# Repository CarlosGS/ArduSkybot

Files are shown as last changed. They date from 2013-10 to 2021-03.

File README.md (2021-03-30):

ArduSkybot  
=====  

**Low cost educational printbot based on Arduino.**  

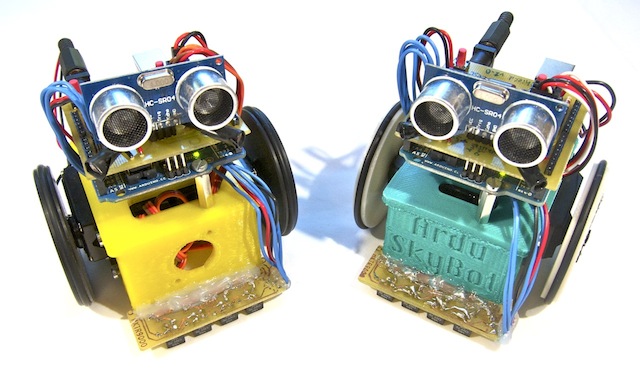
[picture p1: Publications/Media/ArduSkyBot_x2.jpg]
  

Here you will find:  
 * All files and information necessary to build an ArduSkybot.  
 * Arduino code examples for the robot.  
 * Documentation and workshop slides.  
 * Research work about the ArduSkybot (in spanish).  
 * Source files for everything :)  

Video  
--  
You can see the robot being used in the 2012 Summer Workshop:  
**<http://www.youtube.com/watch?v=2o3PmDZZxAQ>**  

License  
--
License (_unless other specified_): **Attribution - Share Alike - Creative Commons (<http://creativecommons.org/licenses/by-sa/3.0/>)**  

Author  
--
Carlos García Saura

Acknowledgement  
--
Based on the MiniSkybot by:  
 * **Juan González Gómez "Obijuan"** (<http://www.iearobotics.com/wiki/index.php?title=Juan_Gonzalez:Main>)  
 * **Alberto Valero Gómez** (<http://iearobotics.com/alberto/doku.php>)  

ArduSkybot  
--
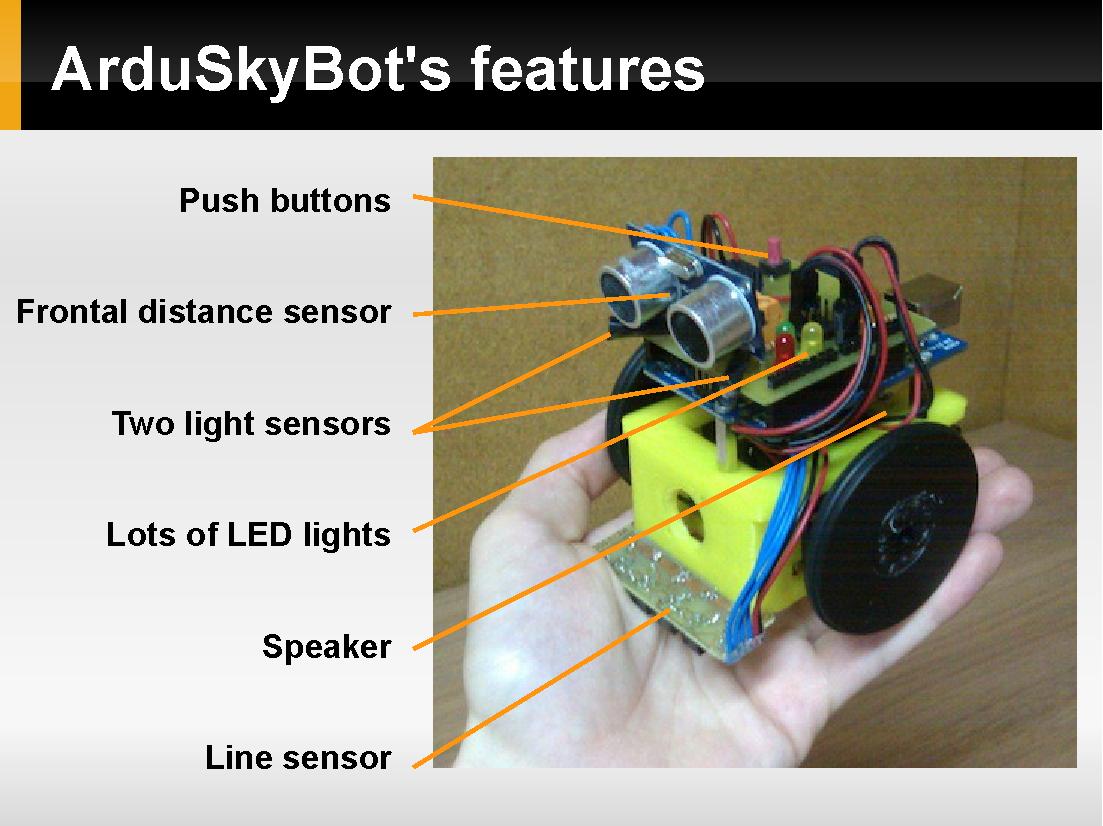
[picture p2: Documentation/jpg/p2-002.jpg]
  
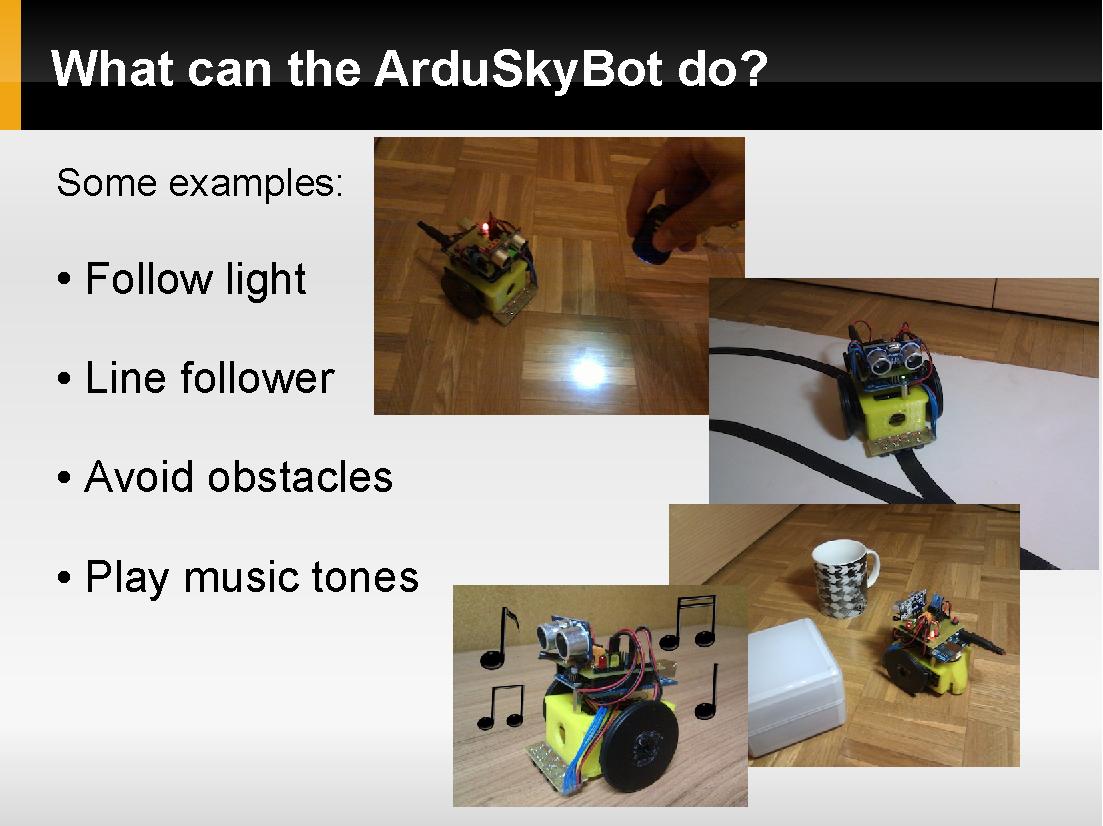
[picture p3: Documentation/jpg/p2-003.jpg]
  
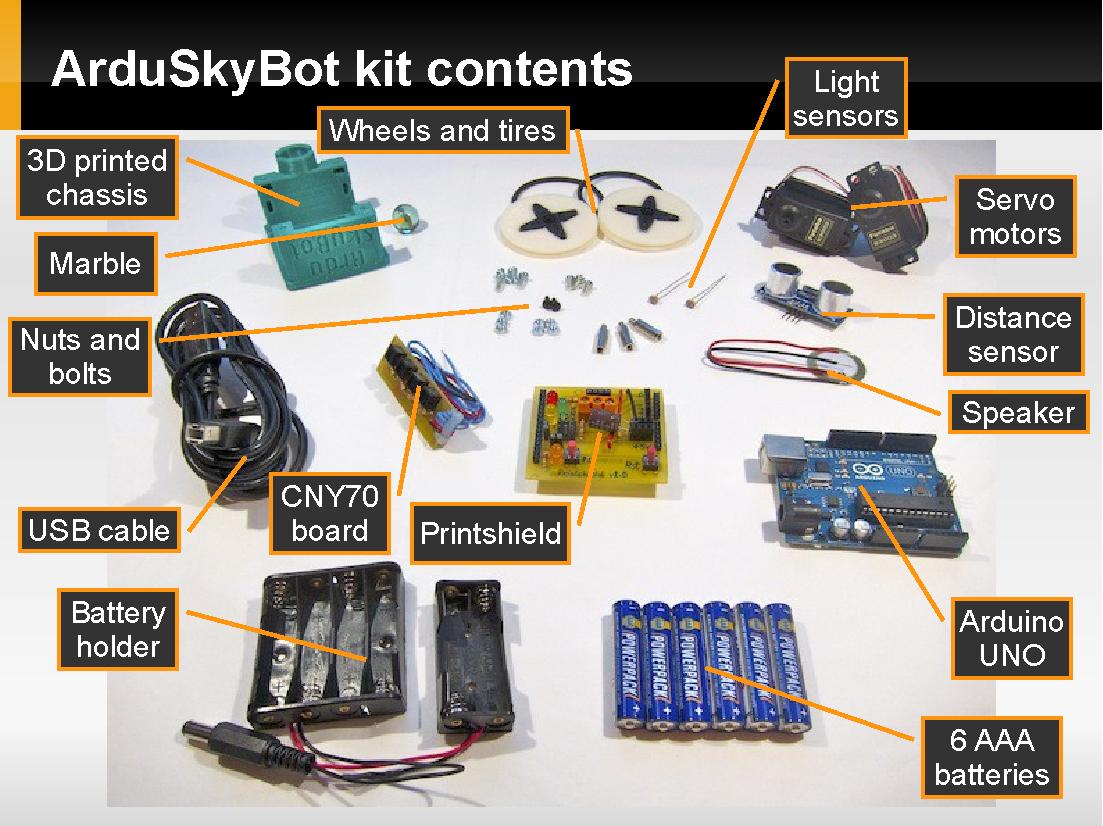
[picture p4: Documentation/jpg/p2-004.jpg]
  
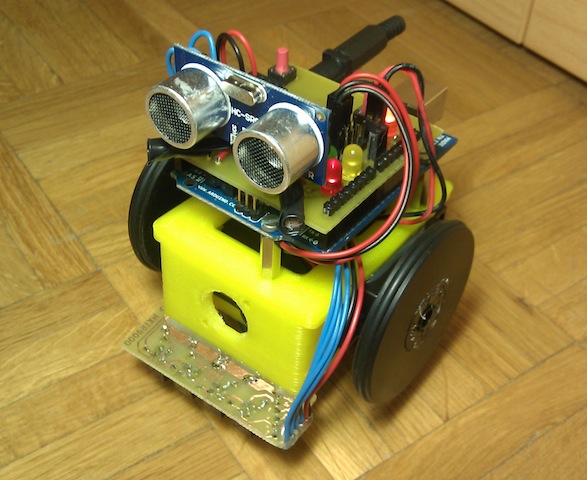
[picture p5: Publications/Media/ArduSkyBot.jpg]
  

Disclaimer  
--
This hardware/software is provided "as is", and you use the hardware/software at your own risk. Under nocircumstances shall any author be liable for direct, indirect, special, incidental, or consequential damages resulting from the use, misuse, or inability to use this hardware/software, even if the authors have been advised of the possibility of such damages.

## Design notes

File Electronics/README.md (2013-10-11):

Electronics for the ArduSkybot  
=====  

_Full instructions (summary below these lines):_
* _Printshield: <https://github.com/carlosgs/ArduSkybot/tree/master/Documentation/1%20-%20Introduction> and <https://github.com/carlosgs/ArduSkybot/tree/master/Documentation/2%20-%20Robot%20assembly>_
* _Line sensor: <https://github.com/carlosgs/ArduSkybot/tree/master/Documentation/4%20-%20Line%20sensor>_

The Printshield for Arduino  
=====  
  
  
  
  

The line sensor board  
=====  
  
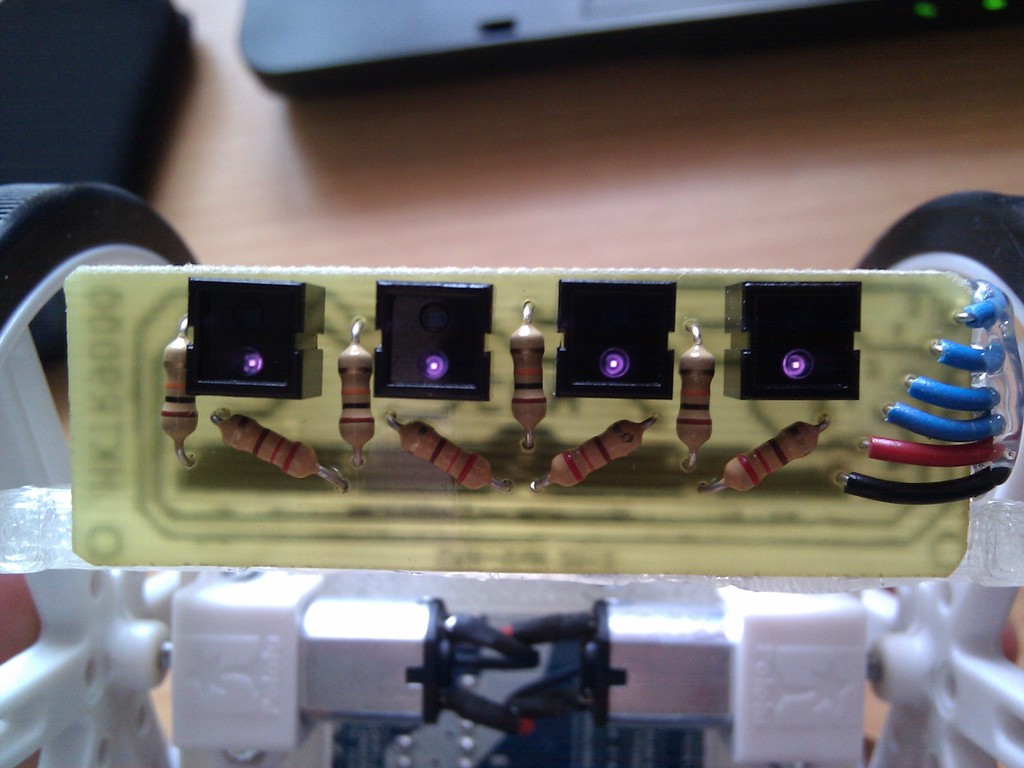
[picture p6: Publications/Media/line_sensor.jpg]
  
  
  


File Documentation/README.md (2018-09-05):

Documentation for the ArduSkybot  
=====  

**In the different folders you will find the instructions for each part of the assembly**  

  

These slides were used in a workshop in Summer 2012, the full description of the workshop is hosted here:  
<https://web.archive.org/web/20150204114811/http://carlosgs.es/2012-summer-workshop>  

Workshop contents  
--  
These slides were used in a workshop in Summer 2012, the full description of the workshop is hosted here: <https://web.archive.org/web/20150204114811/http://carlosgs.es/2012-summer-workshop>  

1. Introduction to robotics with Arduino  
    * Lesson contents:  
        * Basic components of a robot.  
        * What is Arduino and how to program it.  
        * Meet the ArduSkyBot!  
        * You will play music and make LED's blink!  
    * Code (LED blink, tone melody, light harp, servo motor turn and bonus)  
2. Assembling the ArduSkyBot  
    * Lesson contents:  
        * Components of our robot  
        * How to build the ArduSkyBot!  
        * Simple programming examples  
        * You will program your own sequences!  
    * Code (simple ArduSkyBot demo)  
3. Programming the ArduSkyBot  
    * Lesson contents:  
        * Better understanding on how to program for Arduino.  
        * How to use the distance sensor to avoid objects.  
        * Usage of the light sensors to make the ArduSkyBot follow light!  
        * Advanced: while following light, avoid obstacles!  
    * Code  
4. Using the line sensor  
    * Lesson contents:  
        * What is the line sensor and how it works.  
        * How to assemble and test the line sensor.  
        * You will make the ArduSkyBot follow a line!  
        * Advanced: while following a line, avoid obstacles!  
    * Code  

**Jpg images were generated using the following commands:**  
 * gs -sOutputFile=p1-%03d.jpg -dNOPAUSE -dSAFER -sDEVICE=jpeg -dBATCH -r100 2012\ Lesson\ 1\ -\ Introduction\ to\ robotics\ with\ Arduino.pdf
 * gs -sOutputFile=p2-%03d.jpg -dNOPAUSE -dSAFER -sDEVICE=jpeg -dBATCH -r100 2012\ Lesson\ 2\ -\ Assembling\ the\ ArduSkyBot.pdf
 * gs -sOutputFile=p3-%03d.jpg -dNOPAUSE -dSAFER -sDEVICE=jpeg -dBATCH -r100 2012\ Lesson\ 4\ -\ Using\ the\ line\ sensor.pdf

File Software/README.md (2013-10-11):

Software examples for the ArduSkybot  
=====  

These are the examples used for the 2012 Summer Workshop.  

Workshop contents  
--  
1. Introduction to robotics with Arduino  
    * Lesson contents:  
        * Basic components of a robot.  
        * What is Arduino and how to program it.  
        * Meet the ArduSkyBot!  
        * You will play music and make LED's blink!  
    * Code (LED blink, tone melody, light harp, servo motor turn and bonus)  
2. Assembling the ArduSkyBot  
    * Lesson contents:  
        * Components of our robot  
        * How to build the ArduSkyBot!  
        * Simple programming examples  
        * You will program your own sequences!  
    * Code (simple ArduSkyBot demo)  
3. Programming the ArduSkyBot  
    * Lesson contents:  
        * Better understanding on how to program for Arduino.  
        * How to use the distance sensor to avoid objects.  
        * Usage of the light sensors to make the ArduSkyBot follow light!  
        * Advanced: while following light, avoid obstacles!  
    * Code  
4. Using the line sensor  
    * Lesson contents:  
        * What is the line sensor and how it works.  
        * How to assemble and test the line sensor.  
        * You will make the ArduSkyBot follow a line!  
        * Advanced: while following a line, avoid obstacles!  
    * Code  

ArduSkyBot demo code  
--  
Code for demonstrating the basic functionality of the ArduSkyBot.

1. At the beginning the robot will make a sound and the orange LED will light up.
2. Then you can select an option (with the push button):
    * Orange LED: Distance harp
    * Red LED: Line follower
    * Green LED: Light follower (with obstacle avoidance)
    * Yellow LED: Obstacle avoidance
3. Wait for 5 seconds, the robot will make a sound and the selected LED will blink.
4. Press the button to launch the program.

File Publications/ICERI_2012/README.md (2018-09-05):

Publication for ICERI 2012  
=====  

_Carlos García-Saura, Juan González-Gómez (2012) **"Low cost educational platform for robotics, using open-source 3D printers and open-source hardware"**, ICERI2012 Proceedings, pp. 2699-2706. ISBN: 978-84-616-0763-1_  

<https://web.archive.org/web/20150204114839/http://carlosgs.es/Printbots-for-education-at-ICERI-2012>  

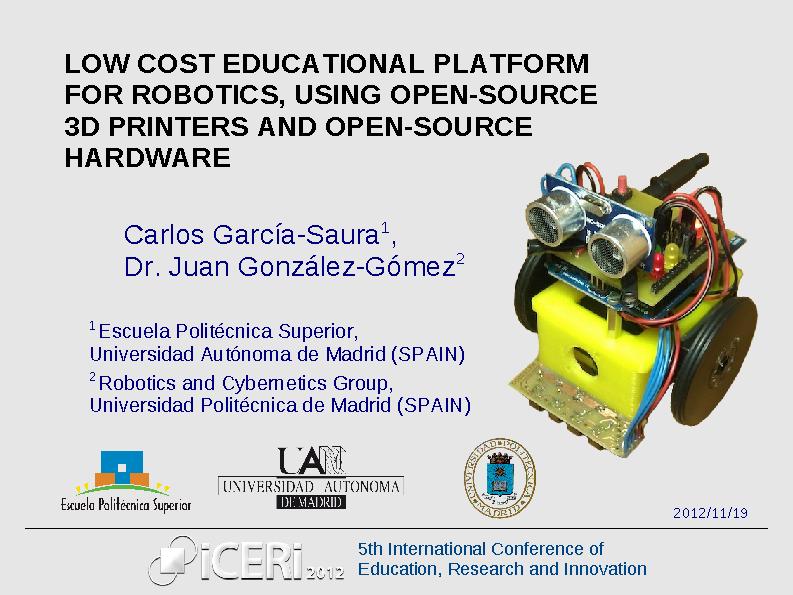
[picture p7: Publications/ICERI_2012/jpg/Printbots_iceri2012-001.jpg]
  
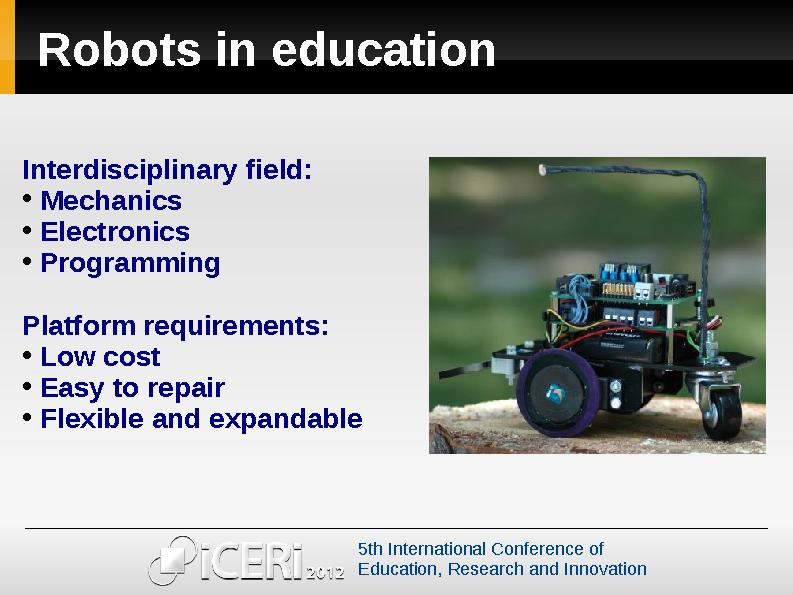
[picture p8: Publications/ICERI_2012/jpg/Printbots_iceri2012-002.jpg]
  
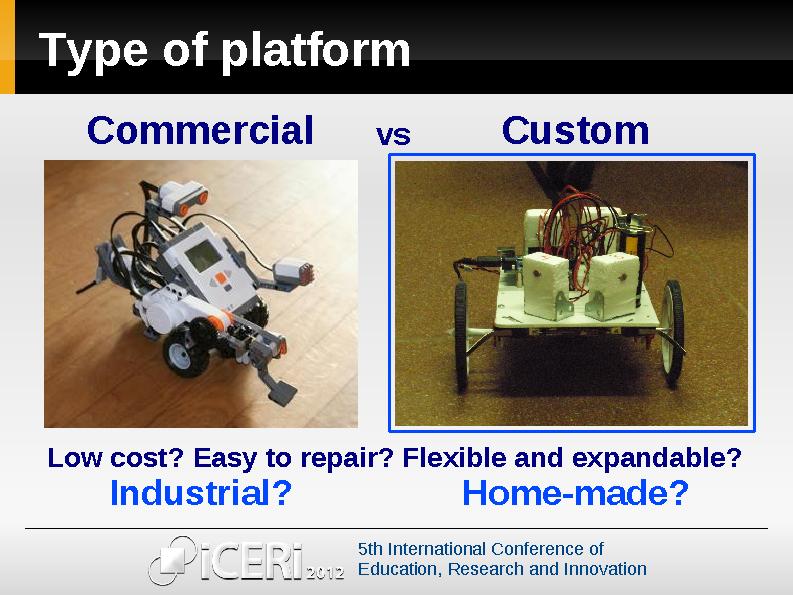
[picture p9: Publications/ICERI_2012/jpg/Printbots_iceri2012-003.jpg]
  
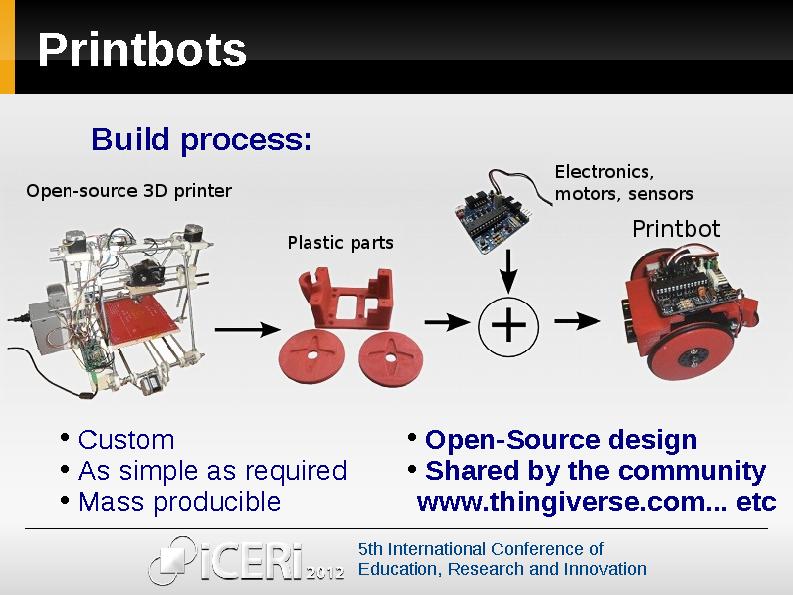
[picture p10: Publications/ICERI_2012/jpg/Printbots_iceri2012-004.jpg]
  
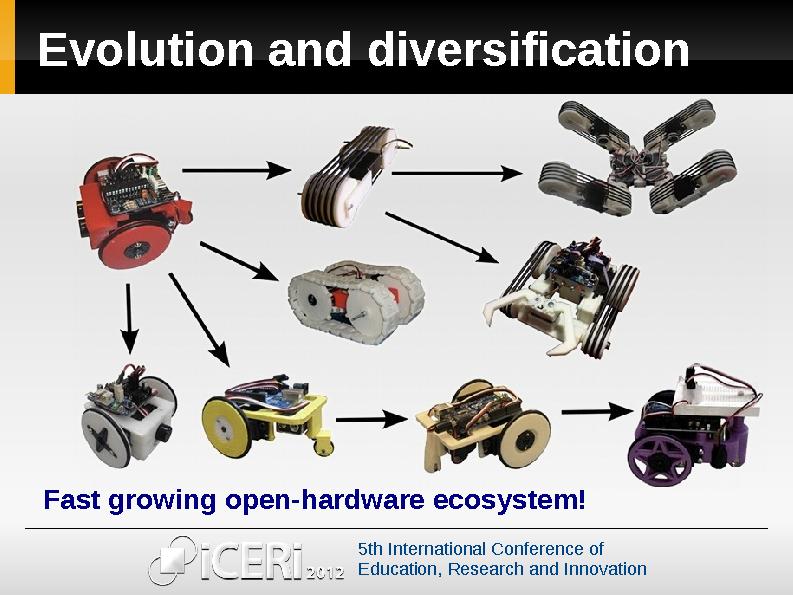
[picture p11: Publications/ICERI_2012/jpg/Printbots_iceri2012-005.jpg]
  
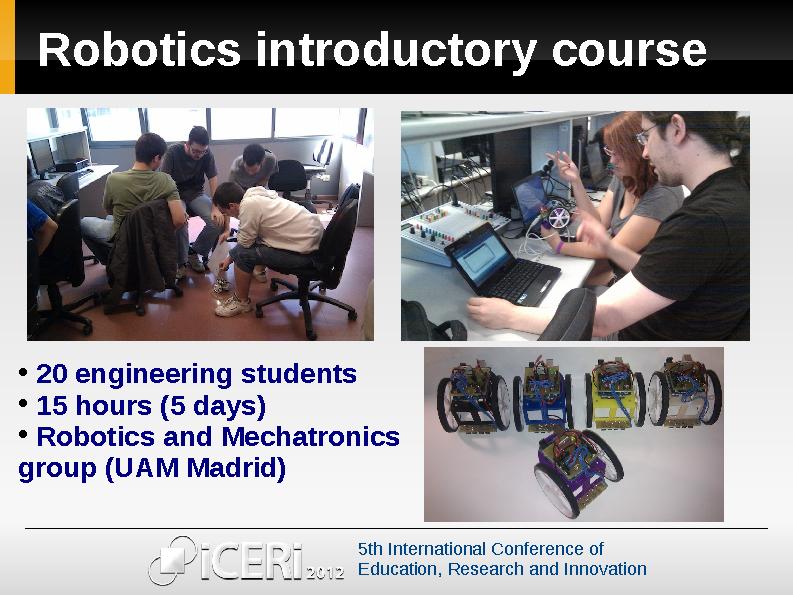
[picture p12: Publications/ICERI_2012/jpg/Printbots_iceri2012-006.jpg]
  
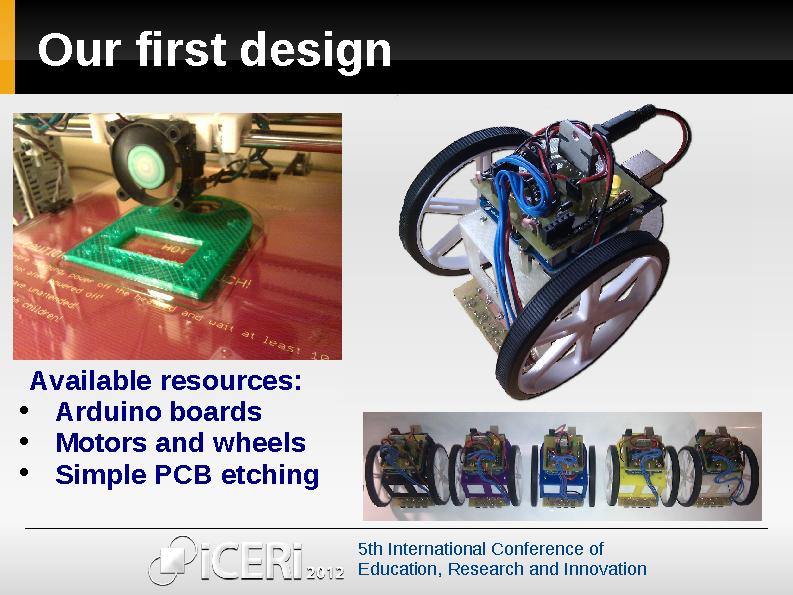
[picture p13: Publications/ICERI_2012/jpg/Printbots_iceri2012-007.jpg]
  
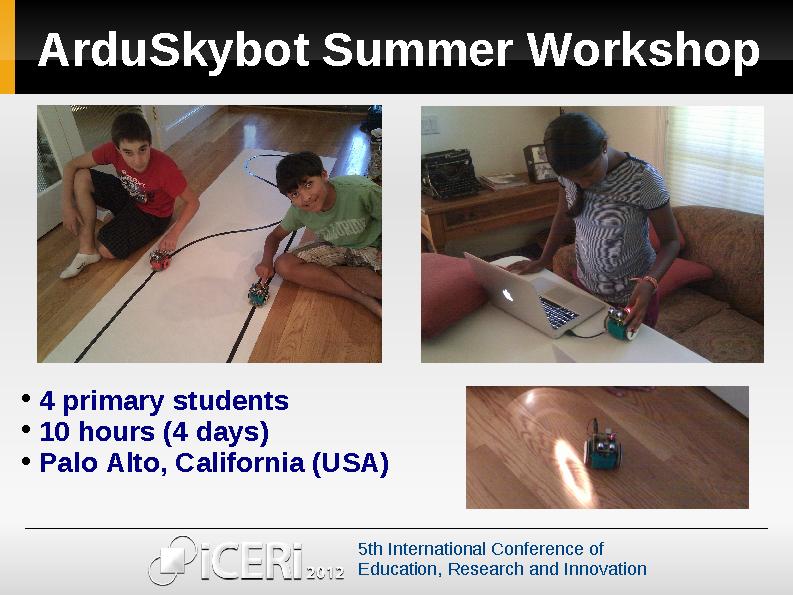
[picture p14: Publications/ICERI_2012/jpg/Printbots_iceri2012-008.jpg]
  
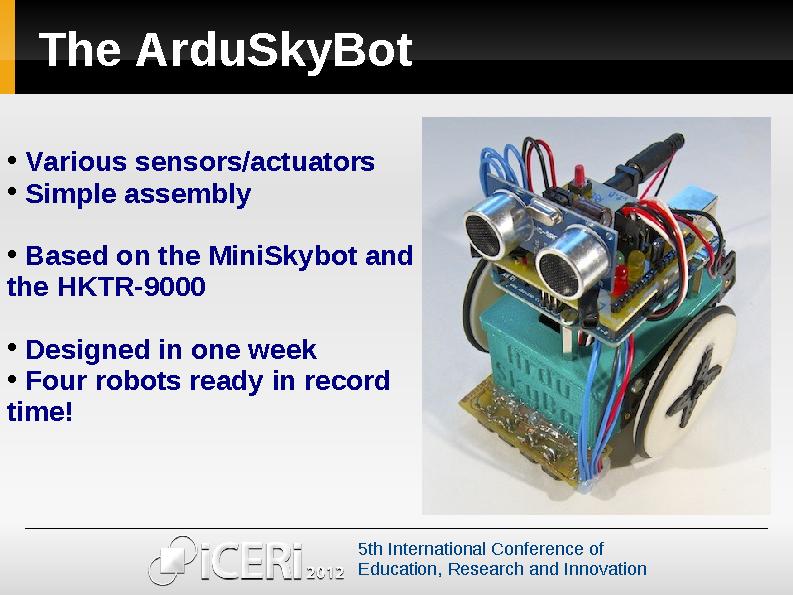
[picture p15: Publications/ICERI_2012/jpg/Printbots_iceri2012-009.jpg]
  
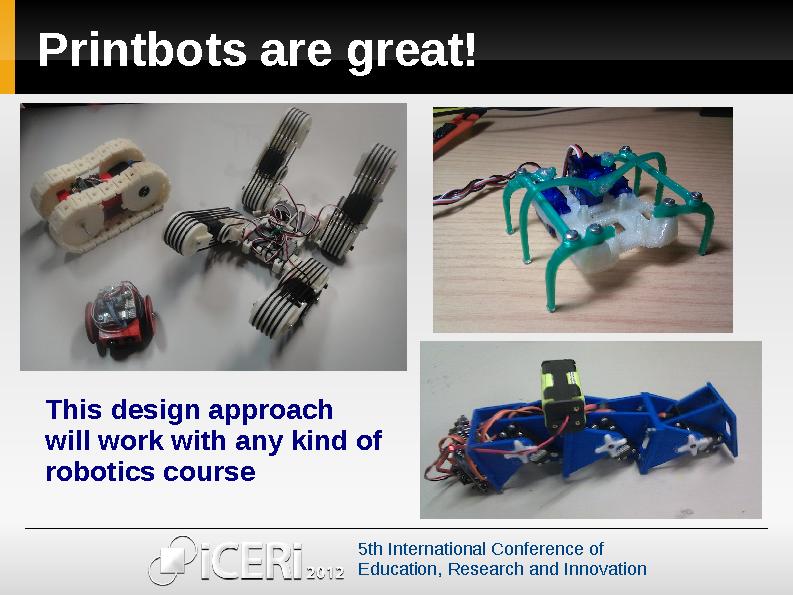
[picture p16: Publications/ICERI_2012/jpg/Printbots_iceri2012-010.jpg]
  
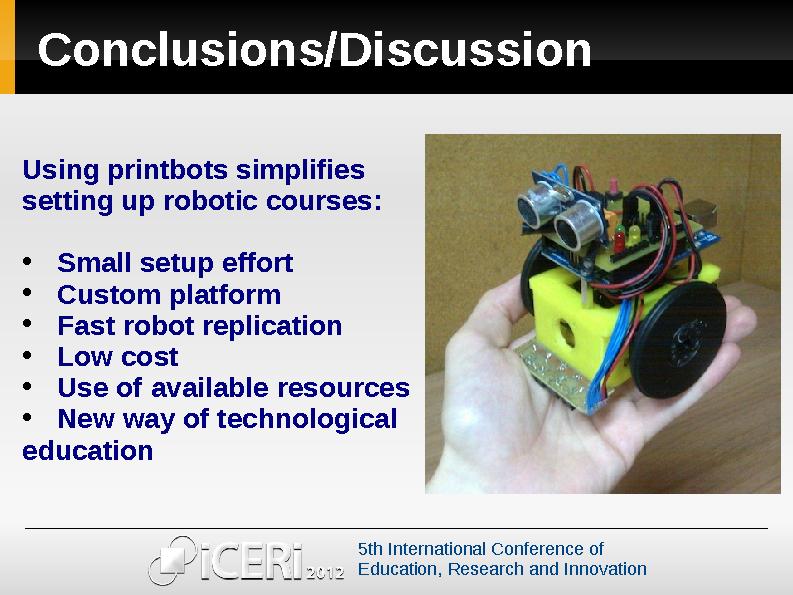
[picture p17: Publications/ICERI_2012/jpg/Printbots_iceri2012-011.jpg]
  
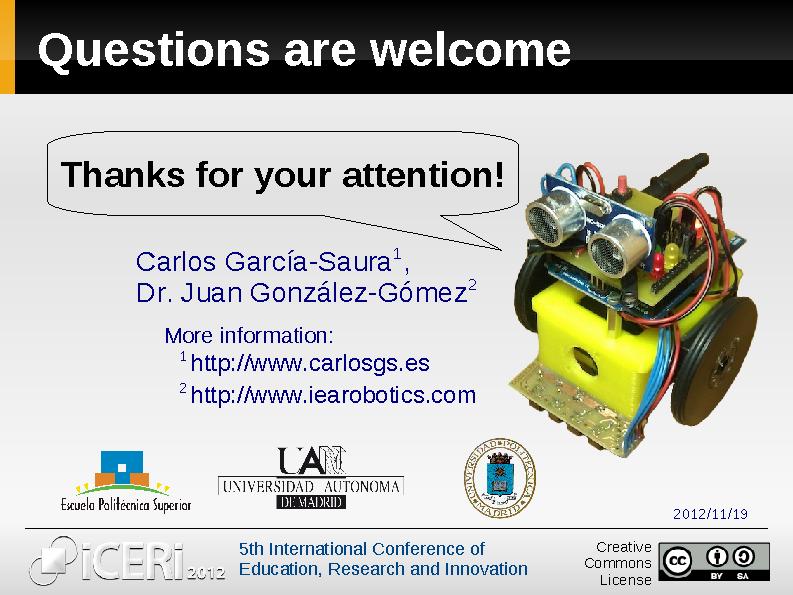
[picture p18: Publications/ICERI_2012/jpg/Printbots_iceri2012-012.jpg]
  

**Jpg images were generated using the following commands:**  
 * gs -sOutputFile=Printbots_iceri2012-%03d.jpg -dNOPAUSE -dSAFER -sDEVICE=jpeg -dBATCH 2012-11-19-ICERI-Printbots_for_education.pdf

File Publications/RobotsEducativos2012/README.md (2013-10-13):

Trabajo de investigación  
=====  
Robots educativos libres, imprimibles y de bajo coste  
--  

Resumen  
--  
La robótica educativa requiere plataformas que sean sencillas de utilizar, siendo a la vez muy completas y manteniendo un precio reducido; pero en muchas ocasiones es necesario dejar de lado al menos uno de estos aspectos.  

En este trabajo de investigación se propone el uso de plataformas educativas de hardware libre.  

Gracias a la tecnología de las impresoras 3D open-source que se han desarrollado en los últimos años, cualquiera puede disponer de una impresora 3D en su casa y fabricar sus propias piezas.  

Los “printbots” son robots libres e imprimibles, es decir, existe una comunidad abierta que comparte todos los diseños y cualquiera puede fabricarlos utilizando una impresora 3D casera.  

Se trata el uso de los printbots como elemento educativo, concretamente el robot HKTR-9000 y de su uso en un taller con estudiantes universitarios.  

Después se proponen mejoras respecto a los printbots educativos, que culminan en el desarrollo del Printshield, una nueva plataforma educativa de hardware abierto y bajo coste basada en Arduino.  

Por último, se demuestra el funcionamiento del ArduSkyBot, un printbot basado en el Printshield, y se exploran sus posibilidades educativas con vista a futuros talleres.  

Más información: <http://carlosgs.es/robots>  

Índice  
--  
* **Introducción**	1  
* **Descripción**	1  
* **Metodología**	2  
* **Justificación**	2  
* **Objetivos**	3  
* **Parte I: Antecedentes**	4  
    1. **La electrónica al alcance de todos: El proyecto Arduino**	4  
        1. El concepto de “Shield”	7  
        2. Software para el diseño electrónico	8  
        3. Sensores	9  
        4. Actuadores	10  
    2. **Impresoras 3D: De bits a objetos**	12  
        1. Materiales utilizados	13  
        2. Proyecto RepRap	14  
        3. Proyecto Clone Wars	14  
        4. OpenScad y la revolución del diseño 3D	18  
    3. **Printbots: Robots libres e imprimibles**	20  
        1. MiniSkybot	21  
        2. Evoluciones	21  
        3. Usando servos como motores de rotación continua	22  
* **Parte II: El robot HKTR-9000**	24  
    1. **Resumen del taller**	24  
        1. Opinión de los estudiantes	25  
    2. **Especificaciones del robot**	26  
        1. CRM-Shield	27  
        2. PCB con los sensores de línea	28  
        3. Sensor de distancia	29  
        4. Conexiones eléctricas	29  
* **Parte III: Mejoras propuestas**	31  
    1. **Soporte para los sensores de luz**	31  
    2. **Integración del sensor de distancia**	32  
    3. **Uso de pulsadores en el shield**	34  
    4. **Integración de un altavoz**	34  
    5. **Uso de servomotores de rotación continua**	35  
    6. **Ruedas y bola de apoyo imprimibles**	36  
* **Parte IV: Diseño experimental**	37  
    1. **Printshield**	37  
        1. Sensores LDR	38  
        2. Sensor de distancia	39  
        3. Servomotores de rotación continua	40  
        4. Pulsadores, diodos LED y altavoz	40  
    2. **Diseño hardware**	41  
    3. **Coste del ArduSkyBot**	44  
    4. **Diseños y documentación realizados**	45  
* **Conclusiones**	46  
* **Agradecimientos**	47  
* **Fuentes, imágenes y licencia**	48  

Licencia del proyecto  
--  
**Attribution - Share Alike Creative Commons license** (<http://creativecommons.org/licenses/by-sa/3.0/>)  

Abstract  
--  
Educational robotics requires platforms that are simple to use, and at the same time full-featured and low-cost; but in many occasions some of these requirements must be left apart.  

This research work proposes using open-hardware educational platforms.  

Thanks to the open-source 3D printing technology that has been developed in recent years, anyone can have a 3D printer at home and manufacture his own parts.  

“Printbots” are open-source robots that are printable, which means that they have an open community that shares every design, and anyone can build them using a 3D printer.  

We also cover the usage of printbots as an educational element. Specifically, the HKTR-9000 robot and its usage on a workshop with college students.  

Then we propose some improvements regarding educational printbots, that culminate with the development of the Printshield, a new educational platform which is Arduino-based, open-hardware and keeps a low cost.  

Finally, we demonstrate the operation of a Printshield-powered printbot: the ArduSkyBot. We also research its educational possibilities regarding future workshops.

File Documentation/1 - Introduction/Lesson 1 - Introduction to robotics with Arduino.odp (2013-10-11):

## Lesson 1 - Introduction

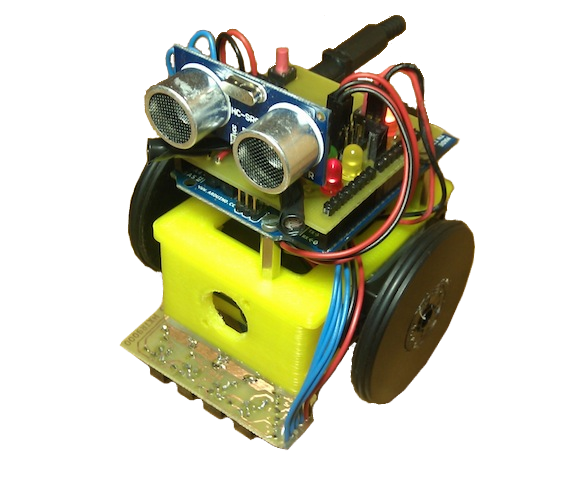
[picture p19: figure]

ArduSkyBot 2012 Summer Workshop

Today you will learn:

- Basic components of a robot.
- What is Arduino and how to program it.
- Meet the ArduSkyBot!
- You will play music and make LED's blink!

Organized by: Carlos García Saura

July-August 2012

## What is a robot?

Autonomous device

that is able to make pre-programmed tasks

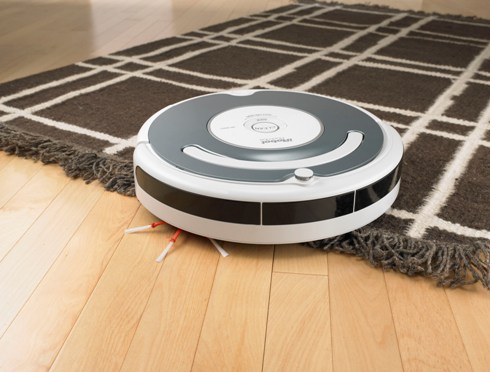
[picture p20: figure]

## Components of a robot

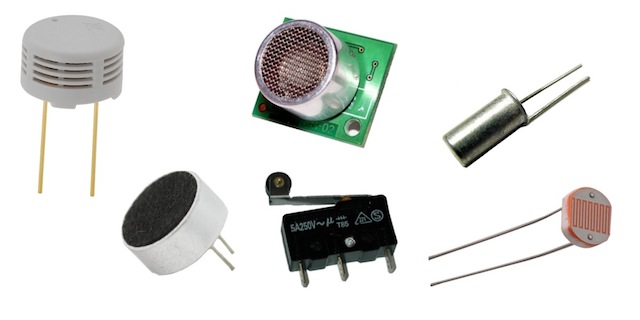
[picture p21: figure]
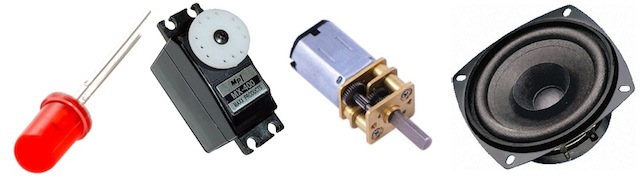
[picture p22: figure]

Sensors

Actuators

## Arduino

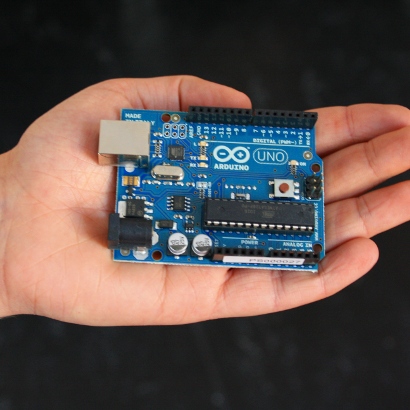
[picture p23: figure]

Open source

electronics platform

It is the “brain”

of our robot!

You can program it with a computer

## Arduino (2)

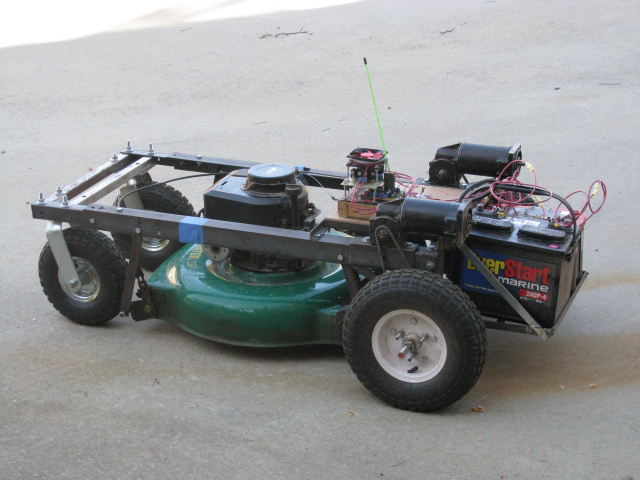
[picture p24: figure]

Automatic toilet flush:

http://www.youtube.com/watch?v=4k899QWsJwI

Arduino paper cat:

http://www.youtube.com/watch?v=ZzZ4_g4YzxY

People make crazy projects

Automatic feeder

RC lawnmower!

## Arduino (3)

We are using Arduino UNO

It has lots of input/output pins

You can connect any kind of sensors and actuators

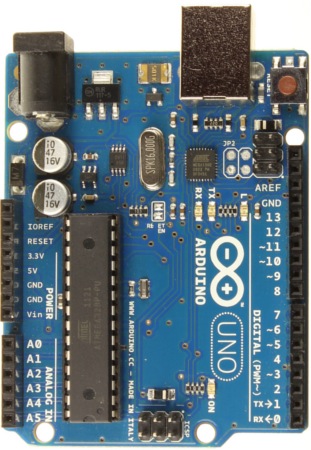
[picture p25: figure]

## Arduino & Printshield

Compact electronics using an Arduino UNO with a Printshield

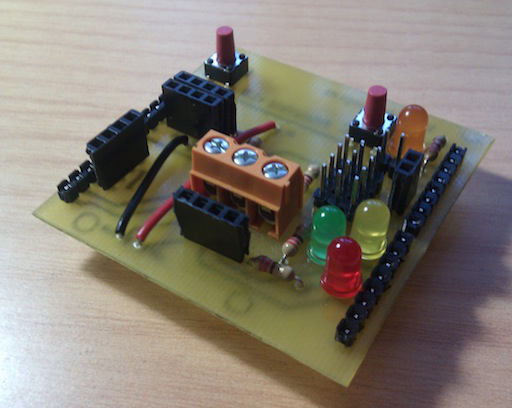
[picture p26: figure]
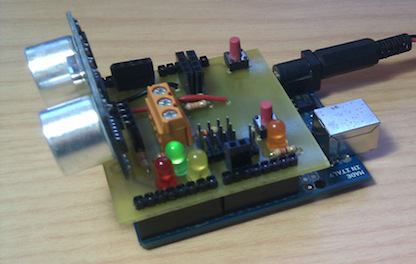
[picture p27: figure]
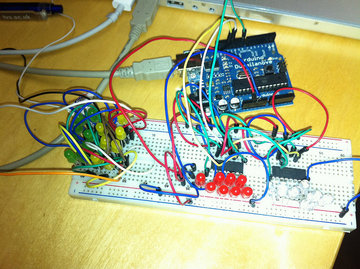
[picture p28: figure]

## Printshield

Connector

for light sensors

LED lights

Connectors

for servo-motors

Connector for

distance sensor

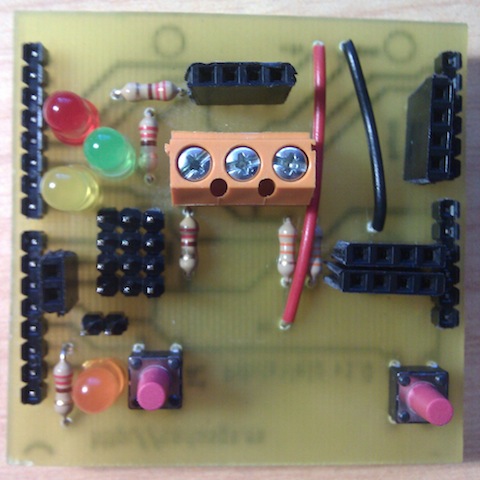
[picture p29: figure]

Connector for

line sensor

+

5V Power line

Another

LED light

Speaker

connector

Push button

Restart/reset

button

## Assembling the Printshield (1)


First we need to insulate the

light sensors with black tape

## Assembling the Printshield (2)


Light sensors need to be screwed

into the orange connector

Then we must plug the Printshield

on the Arduino UNO board


## Plug it into the computer!


Now we just need to load our programs into the board.

Speaker plugs here

USB cable

## Load the “Blink” example

Download more example code from

http://www.carlosgs.es/2012-summer-workshop


## Say hello to the ArduSkyBot!


It features:

Push buttons

Frontal distance sensor

Two light sensors

Lots of LED lights

Line sensor

## What can the ArduSkyBot do?

Some examples:

- Follow light
- Line follower
- Avoid obstacles
- Play music tones


## Tomorrow more!


## License

This work is licensed under the

Attribution - Share Alike

Creative Commons license.

http://creativecommons.org/licenses/by-sa/3.0/

Author:

Carlos García Saura

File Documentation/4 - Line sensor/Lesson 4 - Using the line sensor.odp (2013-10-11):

## Lesson 4 – Using the line sensor


ArduSkyBot 2012 Summer Workshop

Today you will learn:

- What is the line sensor and how it works.
- How to assemble and test the line sensor.
- Make the ArduSkyBot follow a line!

Organized by: Carlos García Saura

July-August 2012

## What is the line sensor?


CNY70 sensors

The software reads “1” if a CNY70 sensor reads white, and “0” when it reads black

## How it works?


RIGHT

LEFT

With four sensors, we can know the position of the black line in the floor.

The read_line() function returns a number that indicates the position of the line.

We can use this number to drive our robot with the robot_heading() function!

## Assembly of the line sensor


## Printshield connections


Line sensor wires:

4

2

3

1

GND

+5V

+

Make sure to connect the wires in the proper order!

## You have finished the ArduSkyBot!


Try to place the wires properly so the robot is compact


## Programming time!


Download the testing and example code from

http://www.carlosgs.es/2012-summer-workshop

## License

This work is licensed under the

Attribution - Share Alike

Creative Commons license.

http://creativecommons.org/licenses/by-sa/3.0/

Author:

Carlos García Saura

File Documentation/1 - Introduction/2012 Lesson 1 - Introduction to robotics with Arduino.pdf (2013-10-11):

## Lesson 1 - Introduction

### ArduSkyBot 2012


### Summer Workshop

Organized by: Carlos García Saura | July-August 2012

Today you will learn:
- Basic components of a robot.
- What is Arduino and how to program it.
- Meet the ArduSkyBot!
- You will play music and make LED's blink!

## What is a robot?


Autonomous device
that is able to make
pre-programmed tasks

## Components of a robot


Sensors

Actuators

## Arduino


Open source
electronics platform

It is the “brain”
of our robot!

You can program
it with a computer

## Arduino (2)


People make
crazy projects

Automatic toilet flush:
http://www.youtube.com/watch?v=4k899QWsJwI
Arduino paper cat:
http://www.youtube.com/watch?v=ZzZ4_g4YzxY

RC lawnmower!

Automatic feeder

## Arduino (3)


We are using Arduino UNO
It has lots of input/output pins

You can connect any kind of sensors and actuators

## Arduino & Printshield


Compact electronics using
an Arduino UNO with a
Printshield

## Printshield

LED lights

Connectors
for servo-motors

Another
LED light

Push button

Restart/reset
button

Speaker connector

5V Power line -

Connector for
line sensor

Connector for
distance sensor

Connector
for light sensors

## Assembling the Printshield (1)


First we need to insulate the light sensors with black tape

## Assembling the Printshield (2)


Light sensors need to be screwed into the orange connector

Then we must plug the Printshield on the Arduino UNO board

## Plug it into the computer!


Now we just need to load our programs into the board.

Speaker plugs here

USB cable

## Load the “Blink” example

Download more example code from http://www.carlosgs.es/2012-summer-workshop


## Say hello to the ArduSkyBot!


It features:

Push buttons

Frontal distance sensor

Two light sensors

Lots of LED lights

Line sensor


What can the ArduSkyBot do?

Some examples:

- Follow light
- Line follower
- Avoid obstacles
- Play music tones


Tomorrow more!


License

This work is licensed under the
Attribution - Share Alike
Creative Commons license.


http://creativecommons.org/licenses/by-sa/3.0/

Author:
Carlos García Saura

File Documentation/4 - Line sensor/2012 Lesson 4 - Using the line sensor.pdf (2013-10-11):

# Lesson 4 – Using the line sensor

# ArduSkyBot 2012


# Summer Workshop

Organized by: Carlos García Saura | July-August 2012

Today you will learn:
- What is the line sensor and how it works.
- How to assemble and test the line sensor.
- Make the ArduSkyBot follow a line!

# What is the line sensor?


CNY70 sensors

The software reads “1” if a CNY70 sensor reads white, and “0” when it reads black

# How it works?


RIGHT | LEFT

With four sensors, we can
know the position of the black line in the floor.

The read_line() function
returns a number that indicates the position of the line.

We can use this number to
drive our robot with the
robot_heading() function!

## Assembly of the line sensor


# Printshield connections


+

4

Line sensor wires:

3
2
1

GND

+5V

Make sure to
connect the wires in
the proper order!

## You have finished the ArduSkyBot!


Try to place the wires properly so the robot is compact

## Programming time!


## Download the testing and example code from http://www.carlosgs.es/2012-summer-workshop

## License

### This work is licensed under the

## Attribution - Share Alike

Creative Commons license.


http://creativecommons.org/licenses/by-sa/3.0/

### Author:

## Carlos García Saura

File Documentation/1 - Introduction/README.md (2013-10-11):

Introduction to the ArduSkybot  
=====  

  
  
  
  
  
  
  
  
  
  
  
  
  
  
  


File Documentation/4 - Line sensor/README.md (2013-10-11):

Line sensor  
=====  

  
  
  
  
  
  
  


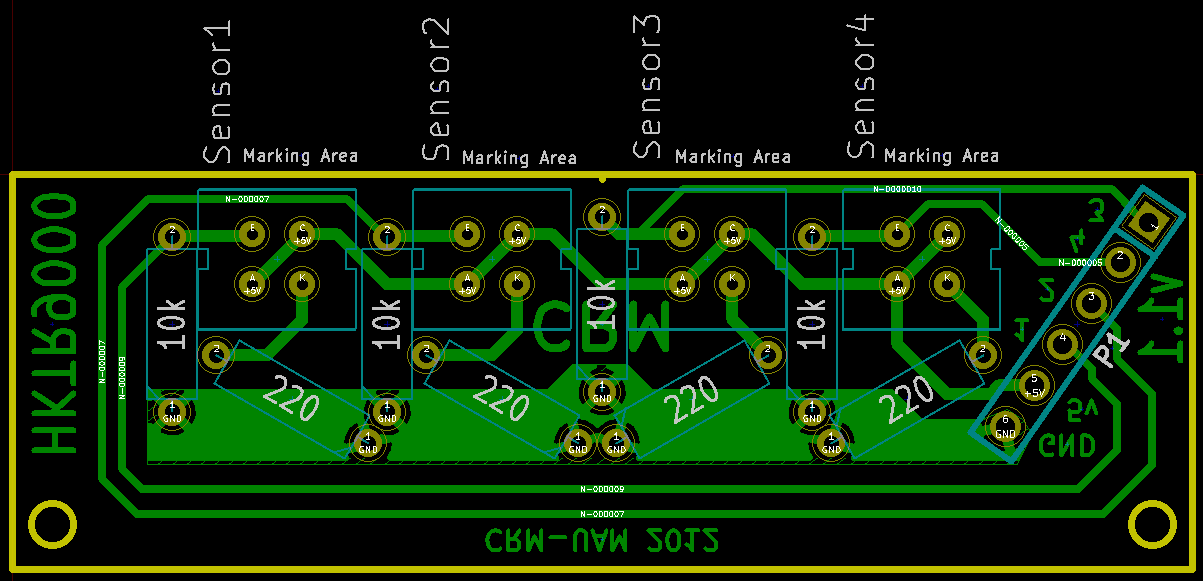
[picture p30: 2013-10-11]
Electronics/CNY70_board_v1.1/board.png

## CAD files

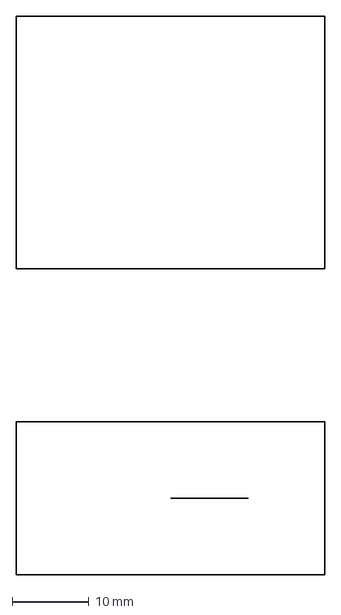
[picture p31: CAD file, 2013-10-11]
Hardware/ArduSkyBot_scad_v2.3/src/futaba3003/futaba-main.dxf
40.3 x 73.0 mm

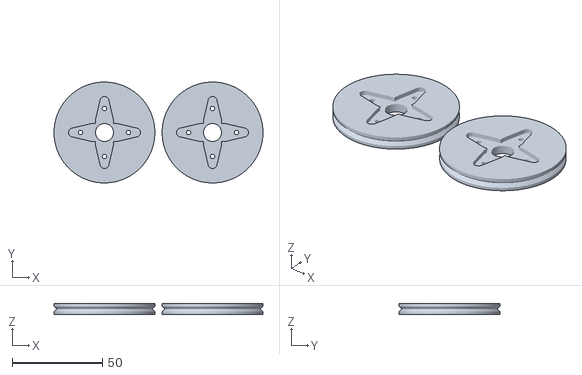
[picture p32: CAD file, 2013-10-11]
Hardware/ArduSkyBot_scad_v2.3/Servo-wheel.stl
116.0 x 56.0 x 6.00

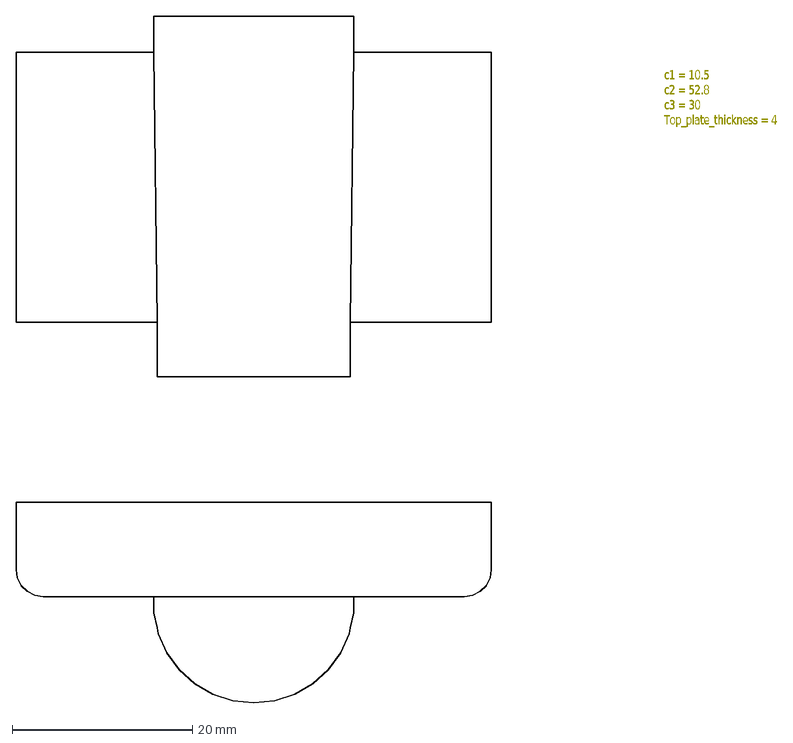
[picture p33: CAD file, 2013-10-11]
Hardware/ArduSkyBot_scad_v2.3/src/doc/rear_doc.dxf
c1 = 10.5 c2 = 52.8 c3 = 30 Top_plate_thickness = 4

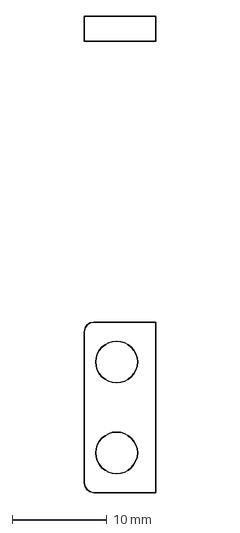
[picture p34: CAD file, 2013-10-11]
Hardware/ArduSkyBot_scad_v2.3/src/futaba3003/futaba-ears.dxf
7.50 x 50.3 mm

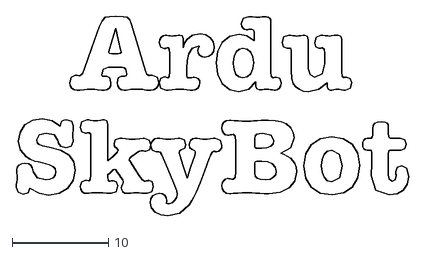
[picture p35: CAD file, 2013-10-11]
Hardware/ArduSkyBot_scad_v2.3/src/Text_ArduSkyBot_original.dxf
40.7 x 20.7

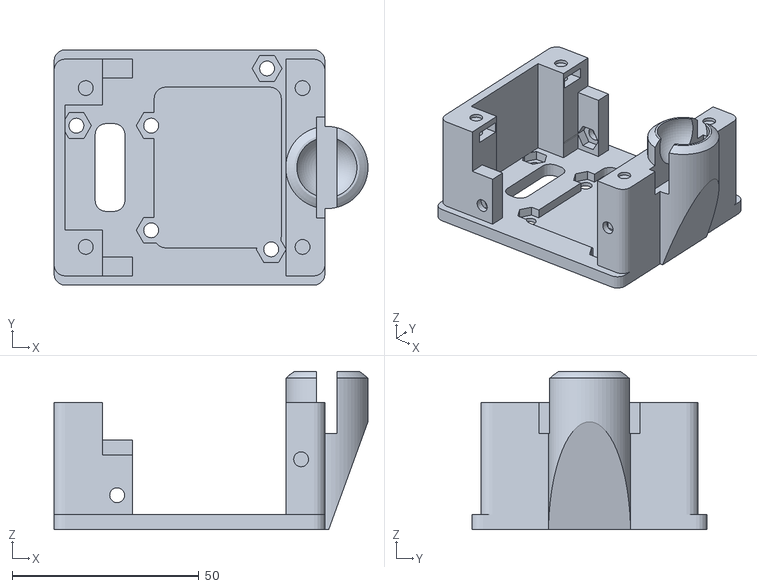
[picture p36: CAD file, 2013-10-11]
Hardware/ArduSkyBot_scad_v2.3/ArduSkyBot_chassis_v2.3.stl
84.0 x 63.0 x 42.3

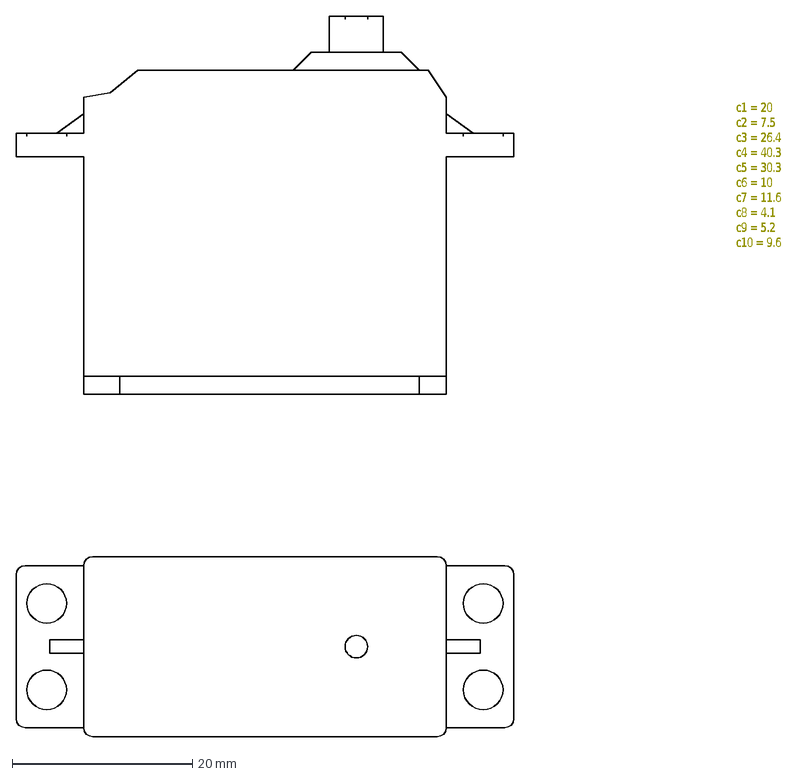
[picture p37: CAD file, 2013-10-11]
Hardware/ArduSkyBot_scad_v2.3/src/doc/futaba-doc2.dxf
c1 = 20 c2 = 7.5 c3 = 26.4 c4 = 40.3 c5 = 30.3 c6 = 10 c7 = 11.6 c8 = 4.1 c9 = 5.2 c10 = 9.6

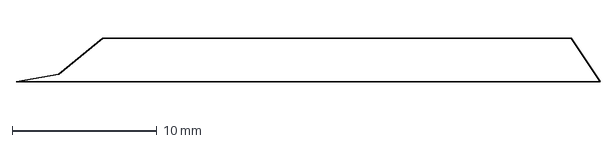
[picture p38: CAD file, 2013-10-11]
Hardware/ArduSkyBot_scad_v2.3/src/futaba3003/futaba-top.dxf
40.3 x 3.00 mm

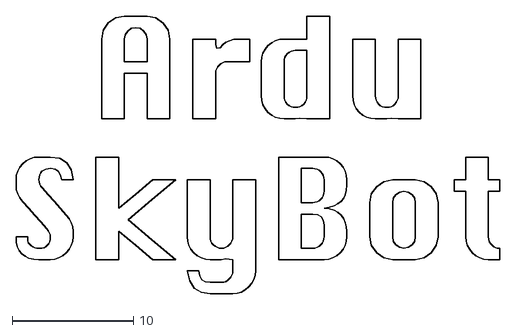
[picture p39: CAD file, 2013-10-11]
Hardware/ArduSkyBot_scad_v2.3/src/Text_ArduSkyBot.dxf
40.0 x 22.9

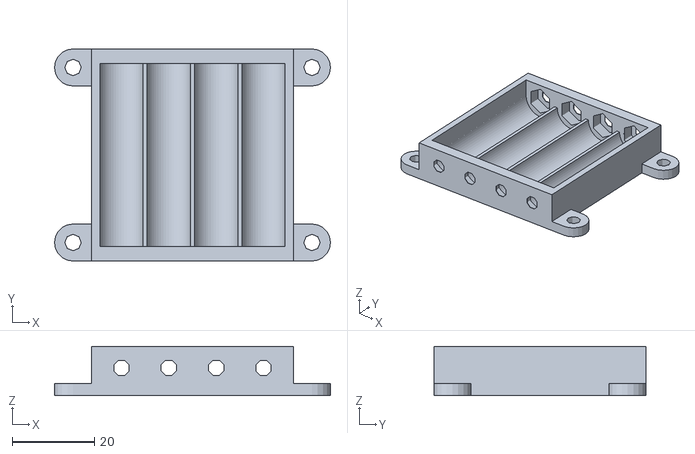
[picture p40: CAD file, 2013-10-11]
Hardware/ArduSkyBot_scad_v2.3/battery_holder.stl
67.0 x 51.5 x 12.0

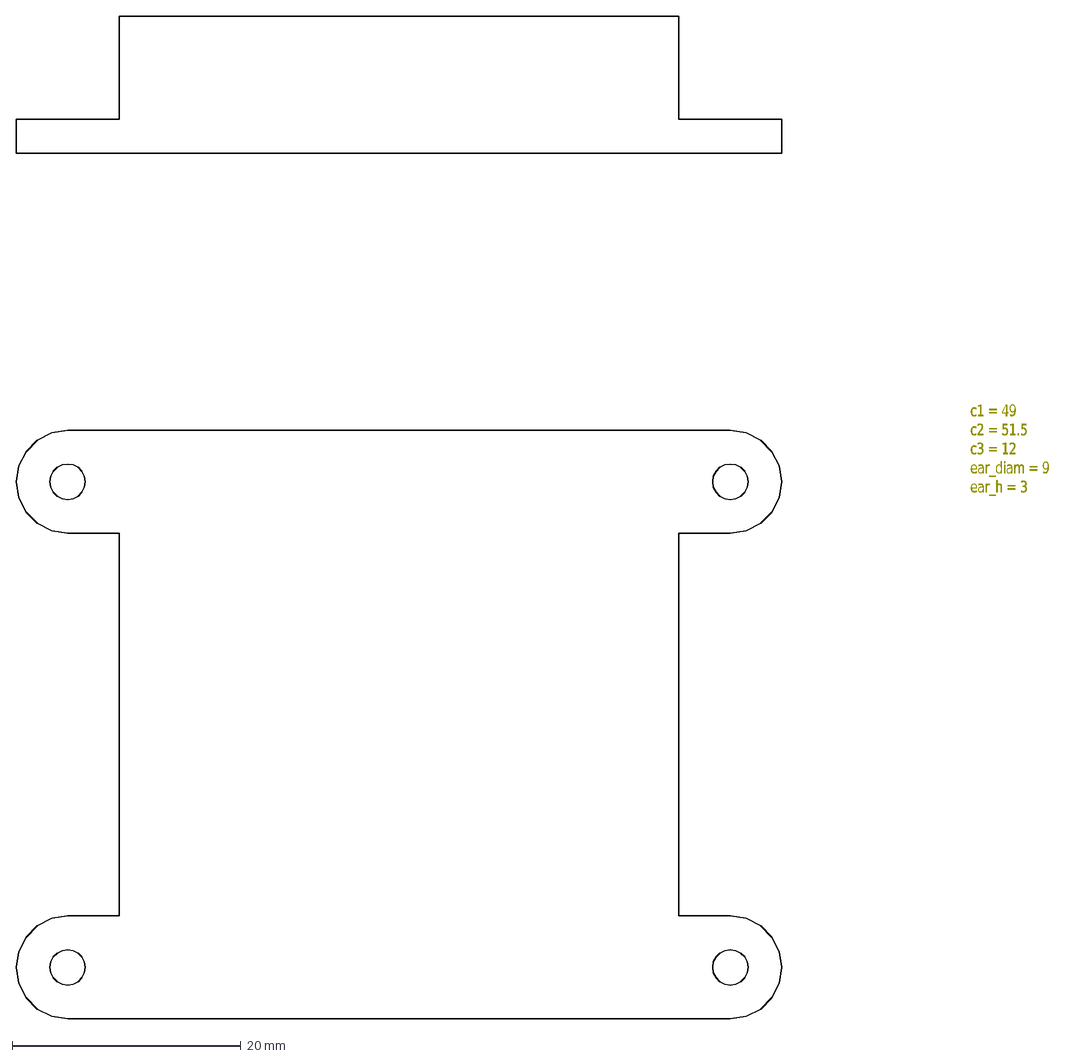
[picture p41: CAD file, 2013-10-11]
Hardware/ArduSkyBot_scad_v2.3/src/doc/battery_holder.dxf
c1 = 49 c2 = 51.5 c3 = 12 ear_diam = 9 ear_h = 3

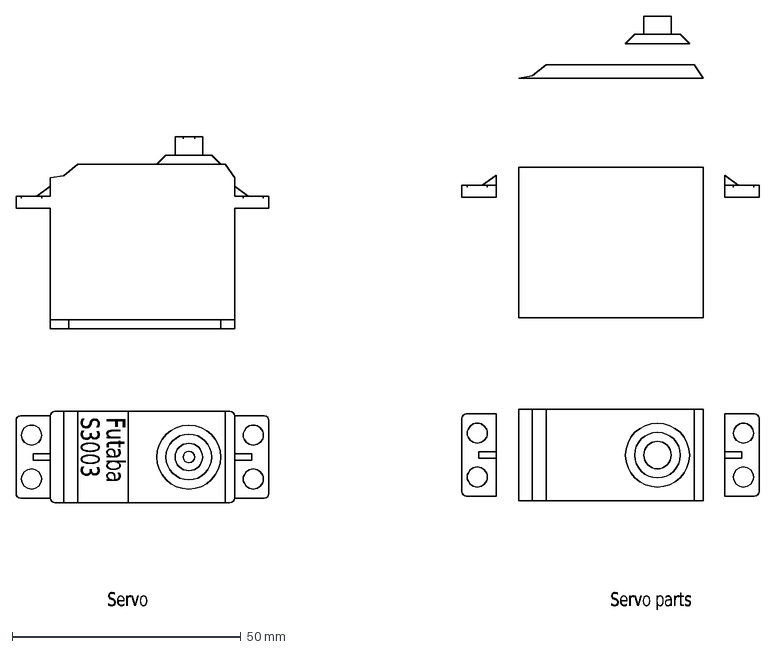
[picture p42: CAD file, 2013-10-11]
Hardware/ArduSkyBot_scad_v2.3/src/futaba3003/futaba-doc1.dxf
Futaba
S3003
Servo
Servo\~parts

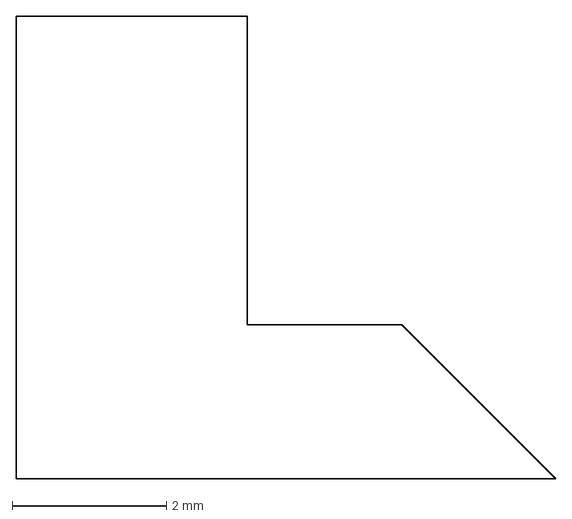
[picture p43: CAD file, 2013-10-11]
Hardware/ArduSkyBot_scad_v2.3/src/futaba3003/futaba-shaft-orig.dxf
7.00 x 6.00 mm

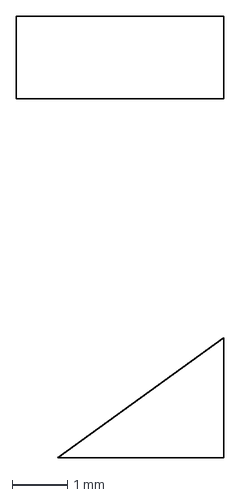
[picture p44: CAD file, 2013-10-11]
Hardware/ArduSkyBot_scad_v2.3/src/futaba3003/futaba-ears2.dxf
3.75 x 8.00 mm

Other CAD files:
Hardware/ArduSkyBot_scad_v2.3/src/futaba3003/futaba.stl
Hardware/ArduSkyBot_scad_v2.3/src/futaba3003/futaba-plate.dxf
Hardware/ArduSkyBot_scad_v2.3/src/configuration.scad
Hardware/ArduSkyBot_scad_v2.3/src/Parameterized_battery_holder.scad
Hardware/ArduSkyBot_scad_v2.3/src/Servo-wheel.scad
Hardware/ArduSkyBot_scad_v2.3/src/battery_holder.scad
Hardware/ArduSkyBot_scad_v2.3/src/fake_ultrasound.scad
Hardware/ArduSkyBot_scad_v2.3/src/functions.scad
Hardware/ArduSkyBot_scad_v2.3/src/futaba3003/futaba.scad
Hardware/ArduSkyBot_scad_v2.3/src/futaba3003/futaba_plate.scad
Hardware/ArduSkyBot_scad_v2.3/src/main.scad

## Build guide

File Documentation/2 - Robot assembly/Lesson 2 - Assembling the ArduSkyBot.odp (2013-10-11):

## Lesson 2 – Robot assembly


ArduSkyBot 2012 Summer Workshop

Today you will learn:

- Components of our robot
- How to build the ArduSkyBot!
- Simple programming examples
- You will program your own sequences!

Organized by: Carlos García Saura

July-August 2012

## ArduSkyBot's features

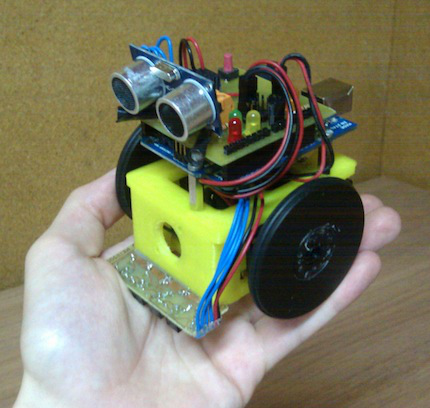
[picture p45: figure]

Push buttons

Frontal distance sensor

Two light sensors

Lots of LED lights

Speaker

Line sensor

## What can the ArduSkyBot do?

Some examples:

- Follow light
- Line follower
- Avoid obstacles
- Play music tones

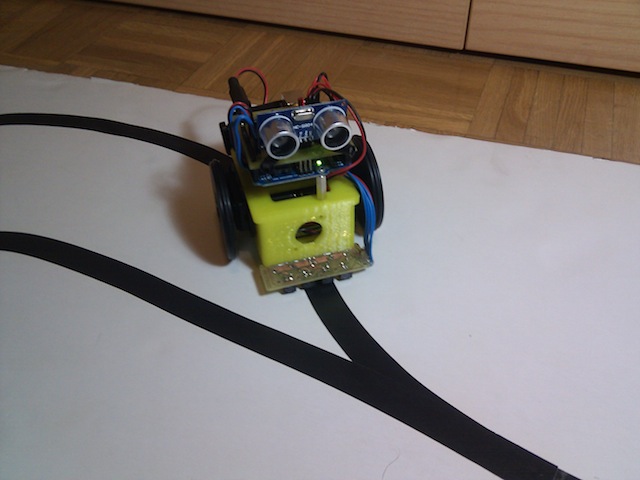
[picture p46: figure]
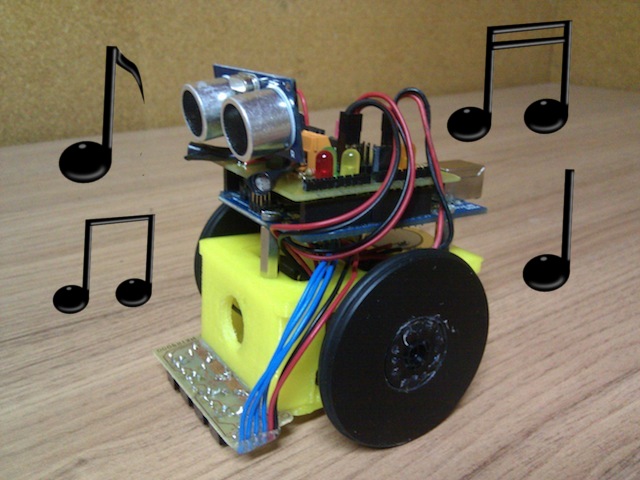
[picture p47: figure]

## ArduSkyBot kit contents

Wheels and tires

Light

sensors

3D printed

chassis

Marble

Nuts and

bolts

Servo

motors

Distance

sensor

Speaker

CNY70

board

USB cable

Battery

holder

Printshield

Arduino

UNO

6 AAA

batteries

## Assembly of the ArduSkyBot (1)

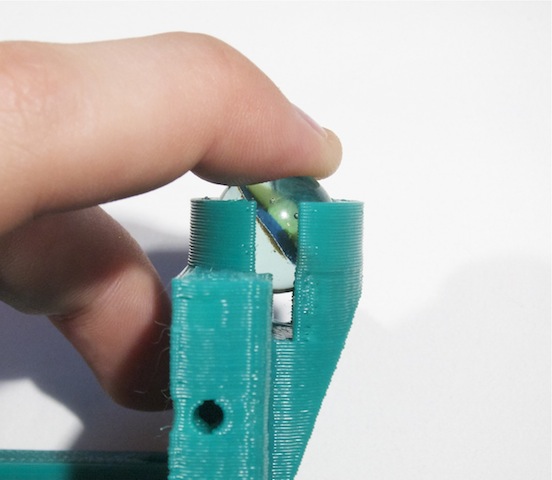
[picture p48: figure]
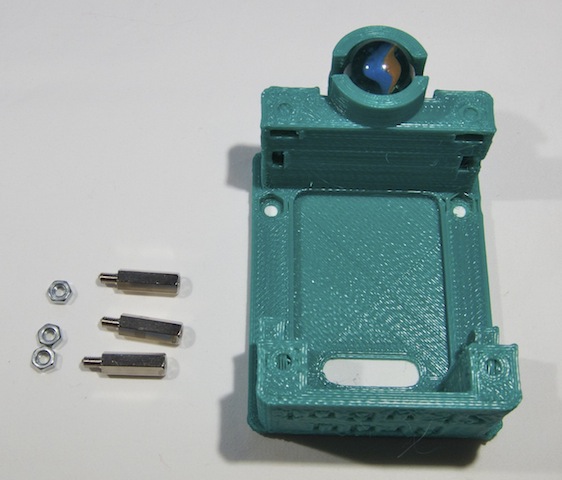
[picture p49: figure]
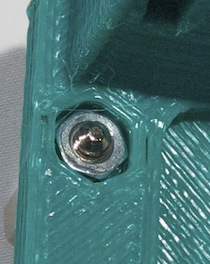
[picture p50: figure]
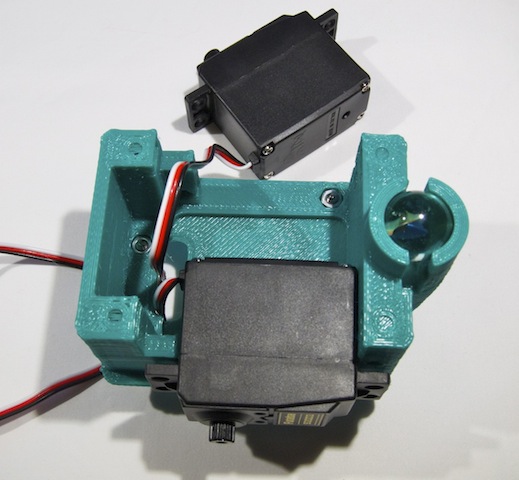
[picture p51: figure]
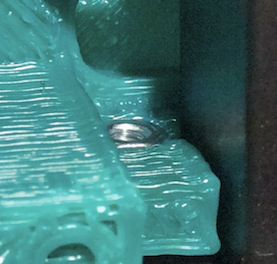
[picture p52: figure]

## Assembly of the ArduSkyBot (2)

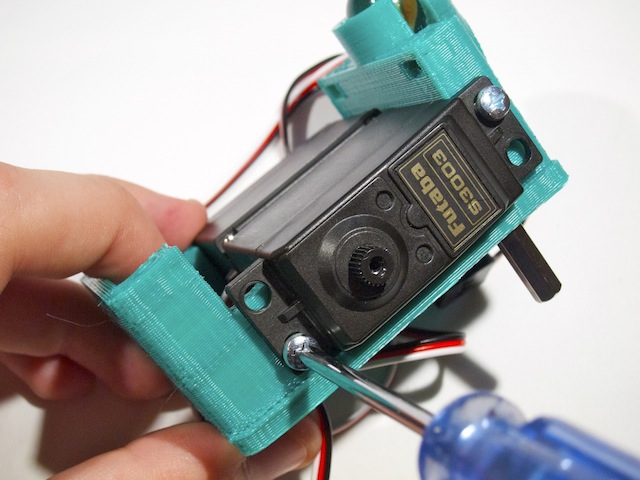
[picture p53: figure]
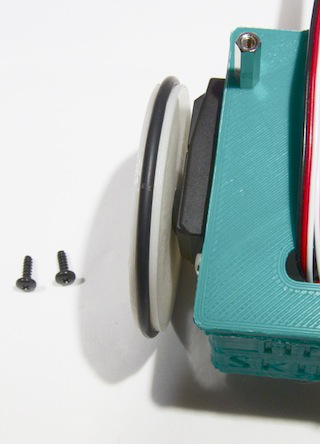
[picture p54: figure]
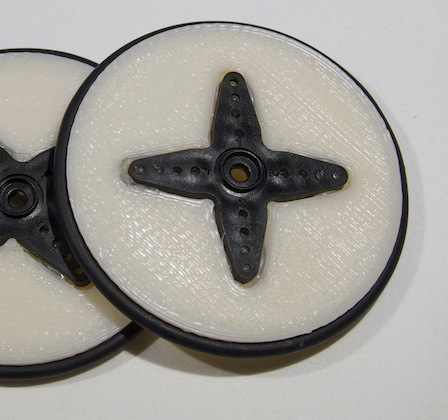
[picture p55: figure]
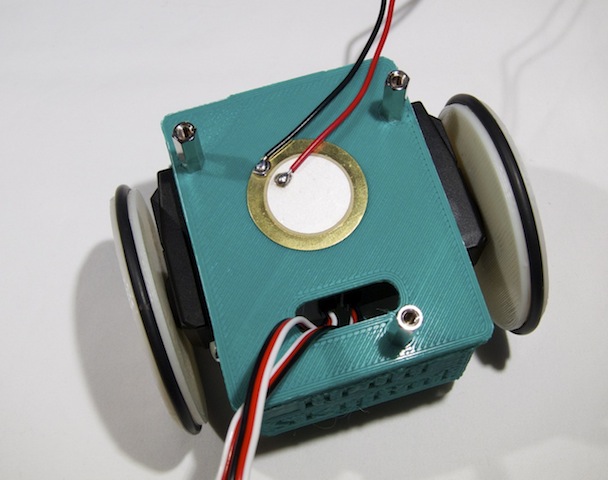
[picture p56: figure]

Note cable

orientation!

## Assembly of the ArduSkyBot (3)

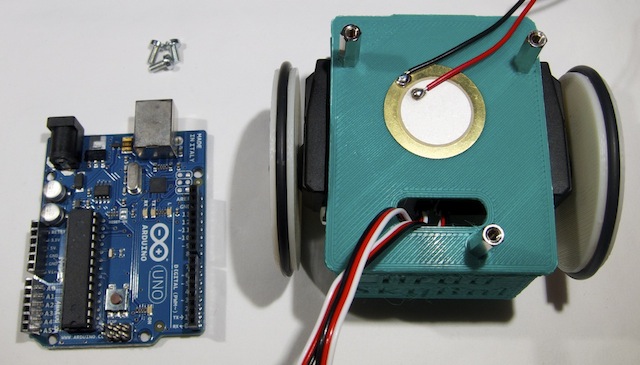
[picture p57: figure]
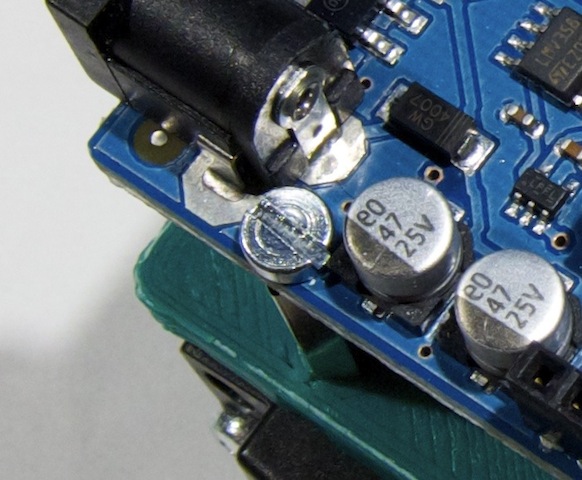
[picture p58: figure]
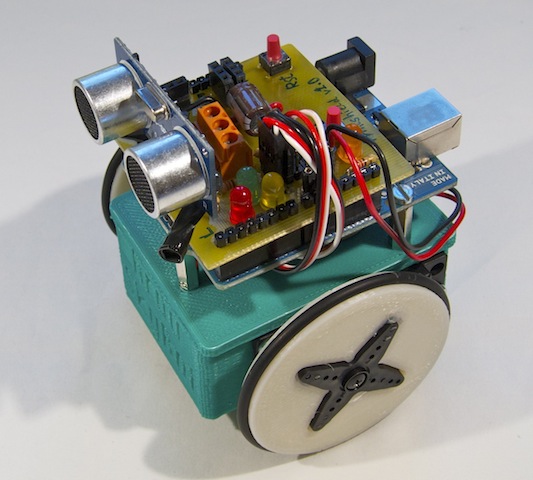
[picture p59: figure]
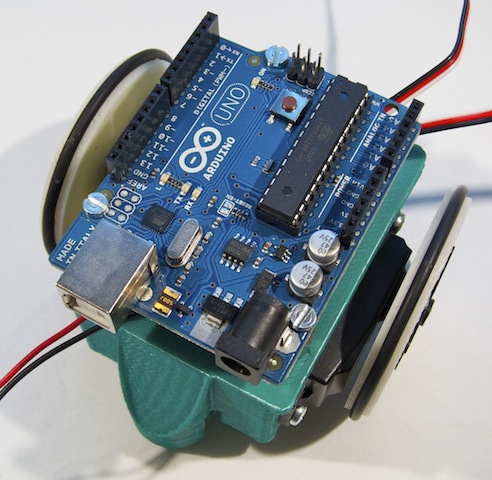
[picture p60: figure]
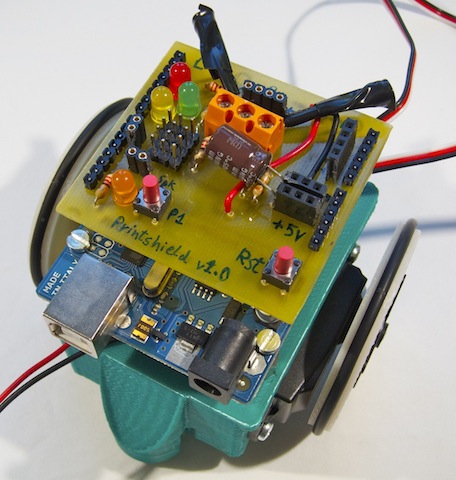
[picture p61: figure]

## Printshield connections

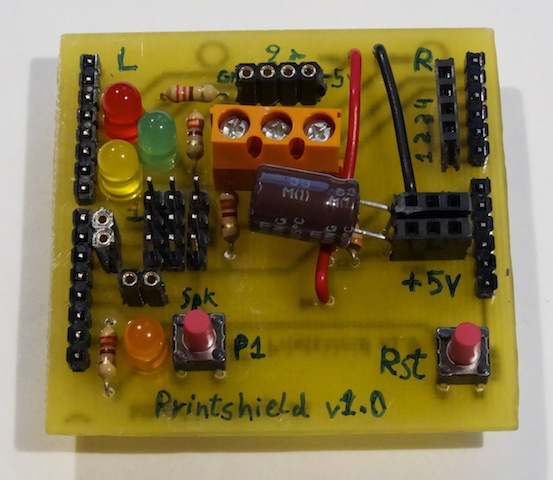
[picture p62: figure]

Distance sensor

Left motor

White/Orange

Cable (signal)

Right motor

+

Speaker

## Assembly of the ArduSkyBot (4)

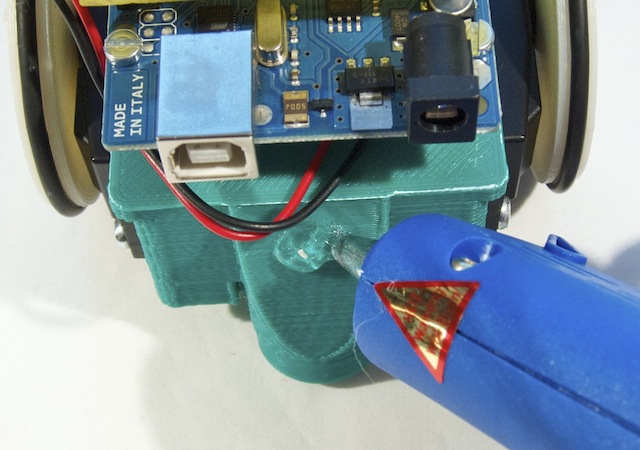
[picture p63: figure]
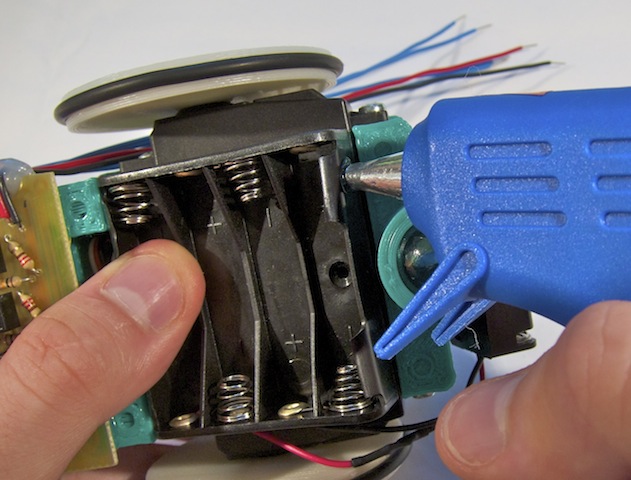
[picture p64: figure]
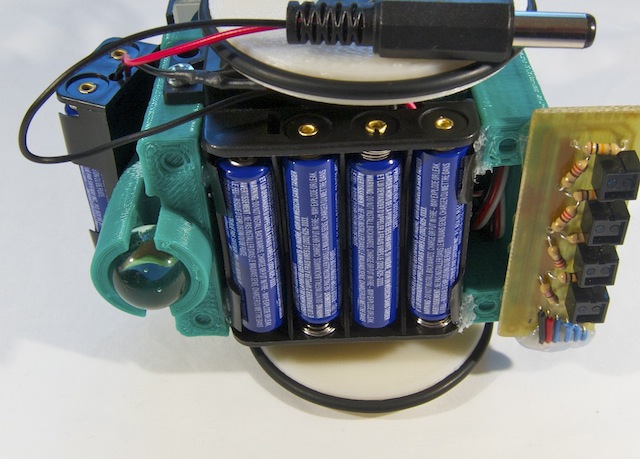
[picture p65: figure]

## You have built an ArduSkyBot!

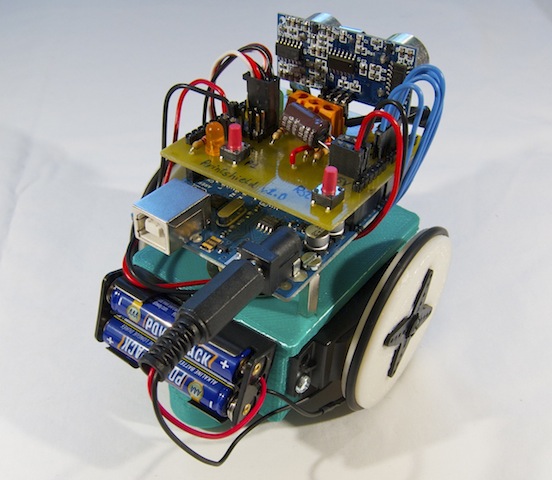
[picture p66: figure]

We will add the line sensor in following lessons!

## Now we can begin with the programming!


Download the example code from

http://www.carlosgs.es/2012-summer-workshop

## License

This work is licensed under the

Attribution - Share Alike

Creative Commons license.

http://creativecommons.org/licenses/by-sa/3.0/

Author:

Carlos García Saura

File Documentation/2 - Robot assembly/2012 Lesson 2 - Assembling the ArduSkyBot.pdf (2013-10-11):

# Lesson 2 – Robot assembly

# ArduSkyBot 2012

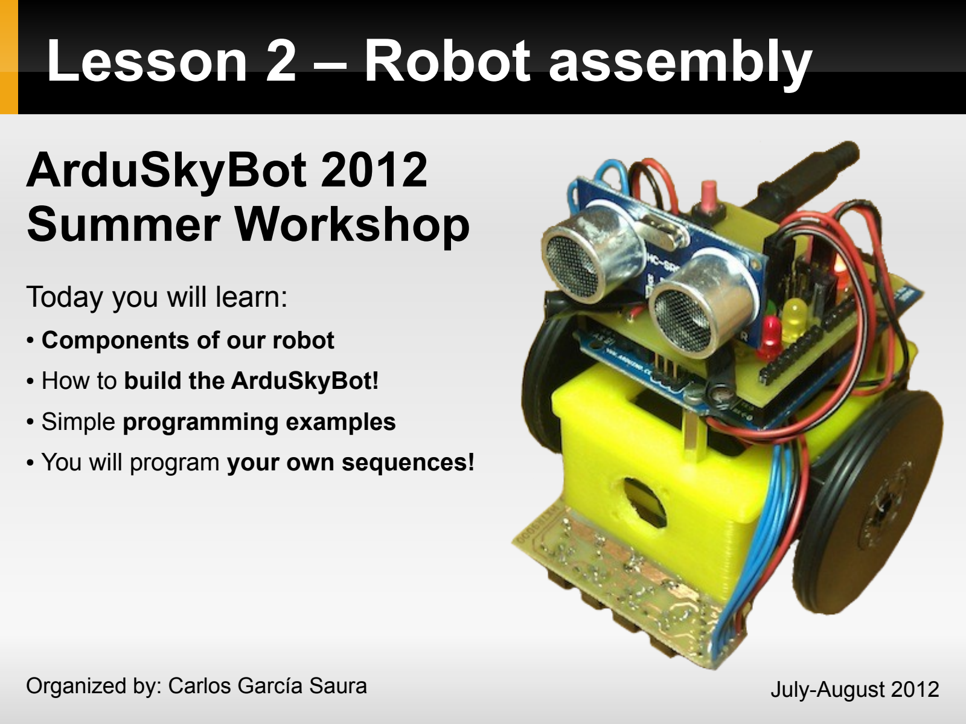
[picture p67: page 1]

# Summer Workshop

Organized by: Carlos García Saura | July-August 2012

Today you will learn:
- Components of our robot
- How to build the ArduSkyBot!
- Simple programming examples
- You will program your own sequences!

# ArduSkyBot's features

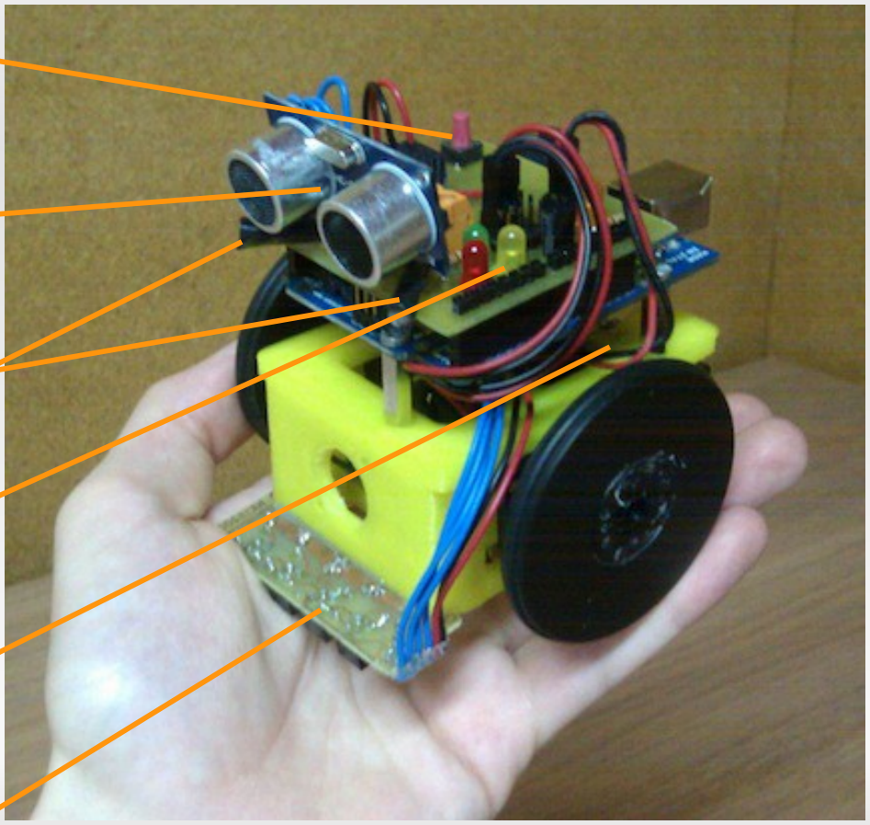
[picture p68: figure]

Push buttons

Frontal distance sensor

Two light sensors

Lots of LED lights

Speaker

Line sensor

## What can the ArduSkyBot do?

### Some examples:

## - Follow light

## - Line follower

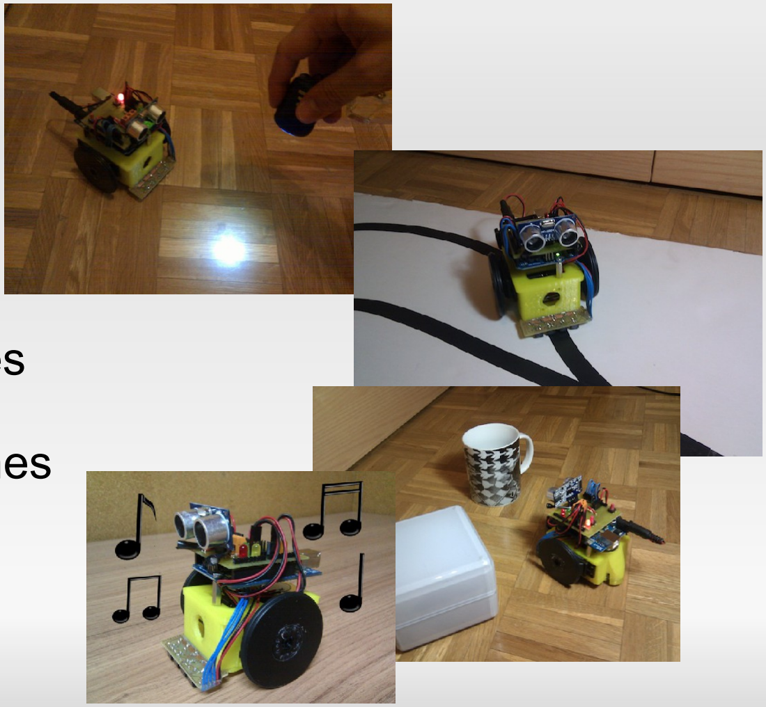
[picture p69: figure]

## - Avoid obstacles

## - Play music tones

## ArduSkyBot kit contents

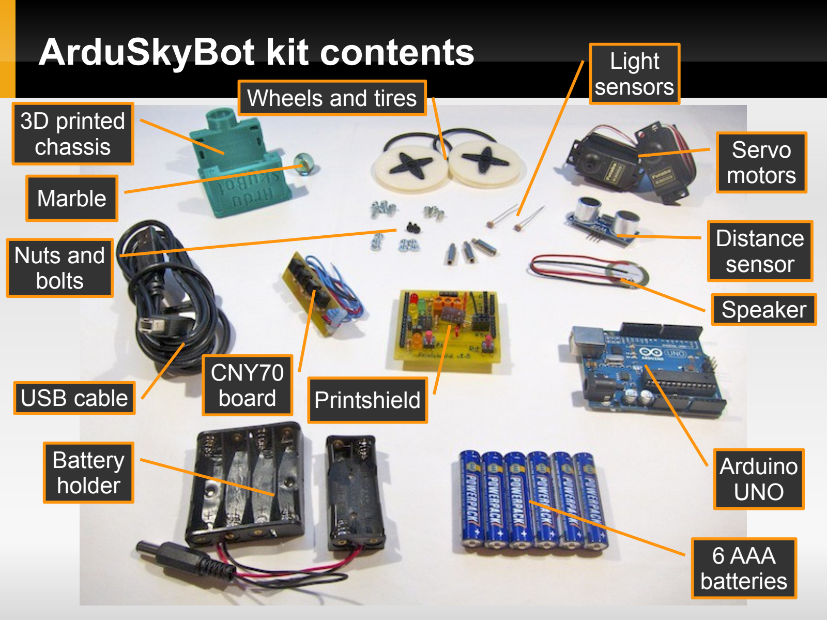
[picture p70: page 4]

3D printed
chassis

Marble

USB cable

Battery
holder

6 AAA
batteries

Arduino
UNO

Printshield

CNY70
board

Wheels and tires

Speaker

Distance
sensor

Servo
motors

Light
sensors

Nuts and
bolts

## Assembly of the ArduSkyBot (1)

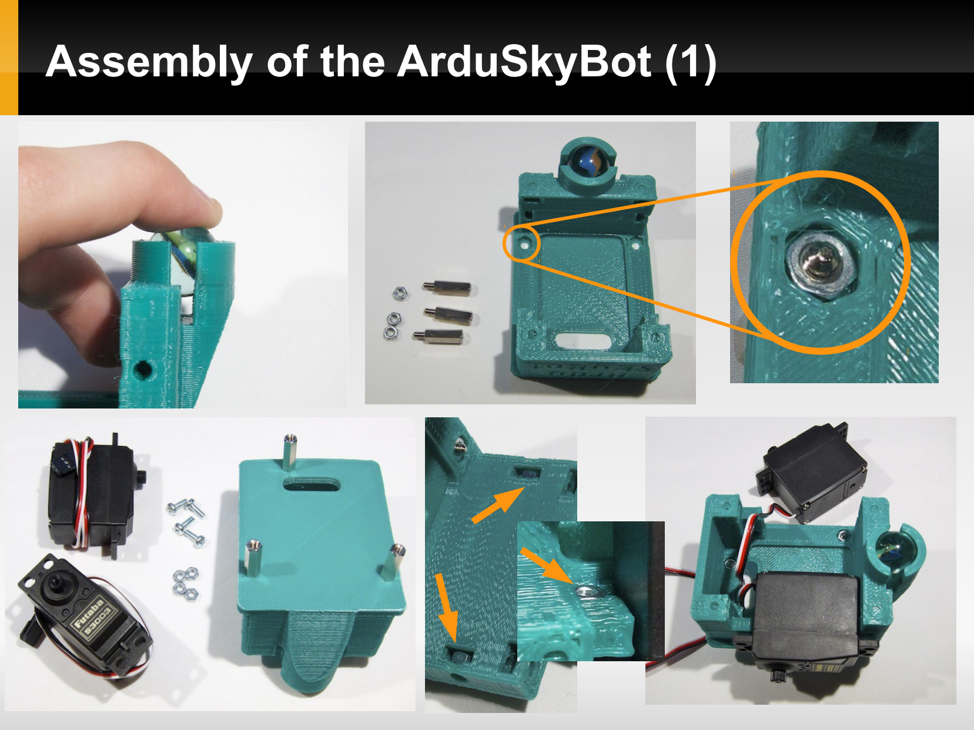
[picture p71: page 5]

## Assembly of the ArduSkyBot (2)

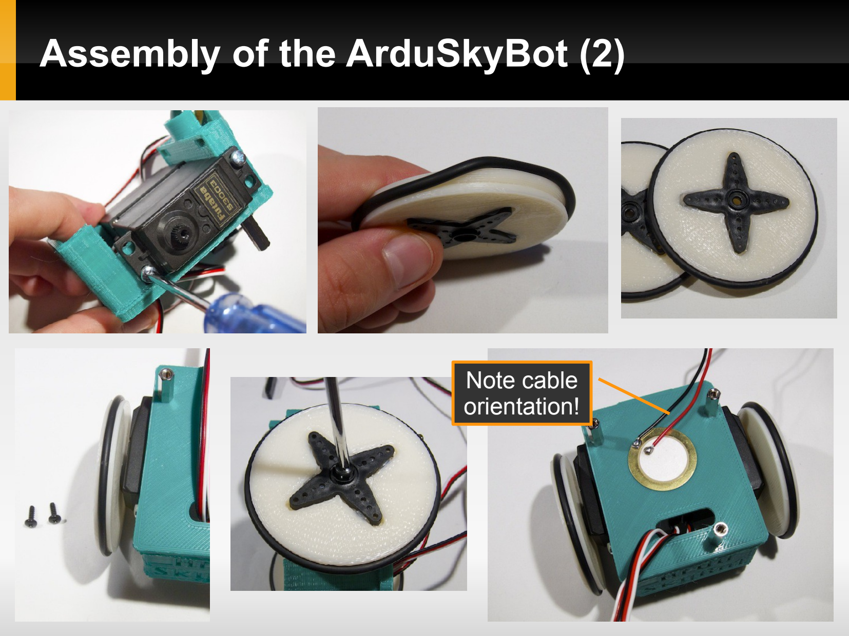
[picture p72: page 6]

Note cable
orientation!

## Assembly of the ArduSkyBot (3)

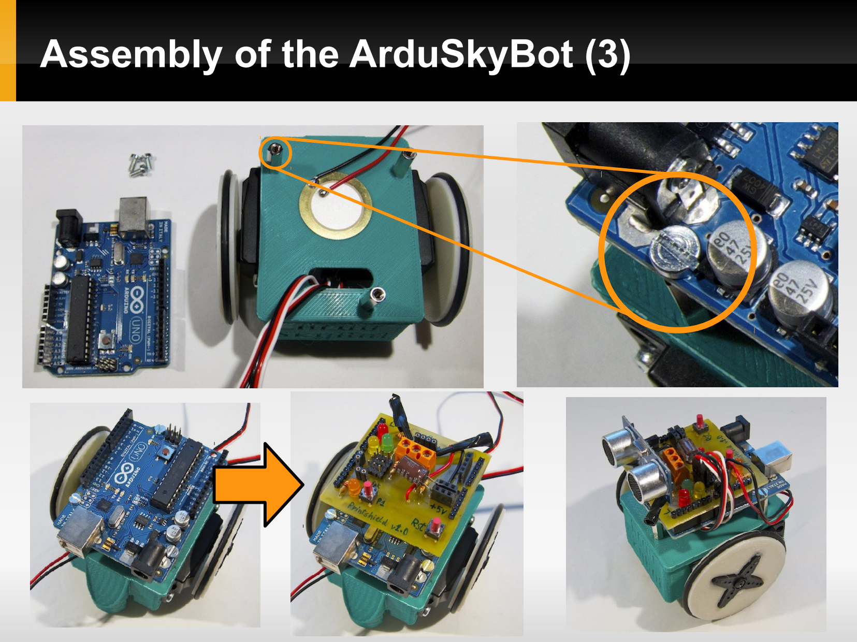
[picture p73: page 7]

# Printshield connections

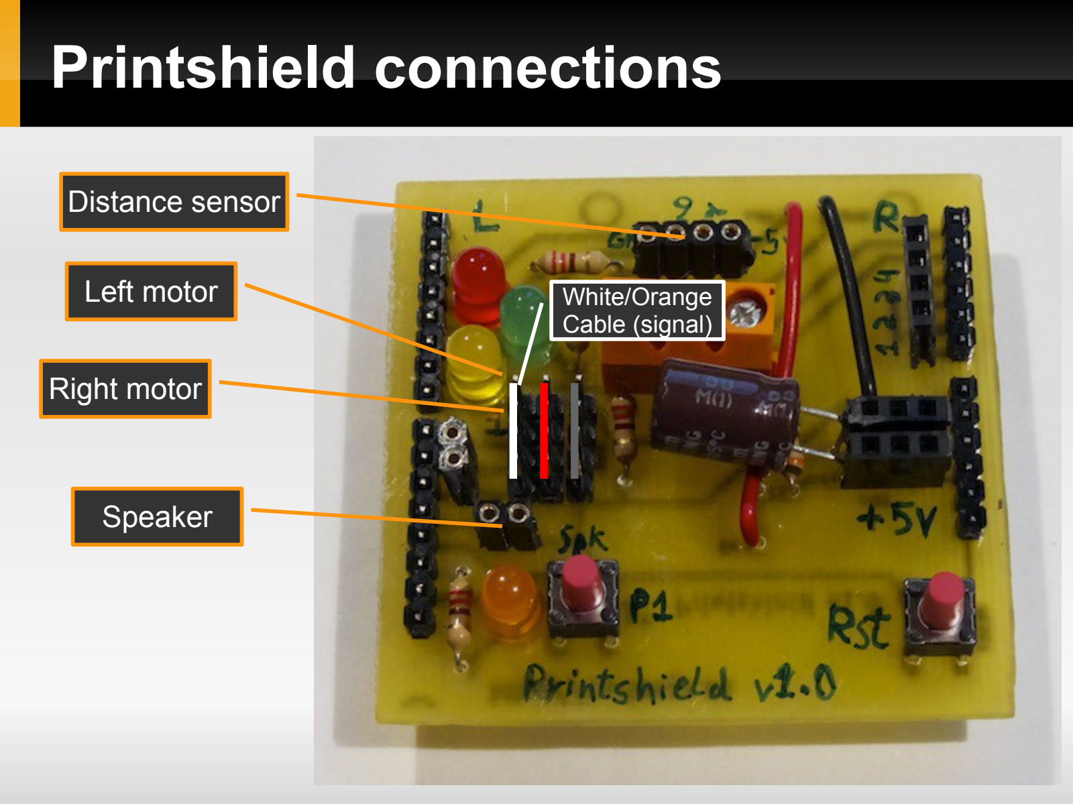
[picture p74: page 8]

+

Left motor

Right motor

Speaker

Distance sensor

White/Orange
Cable (signal)

## Assembly of the ArduSkyBot (4)

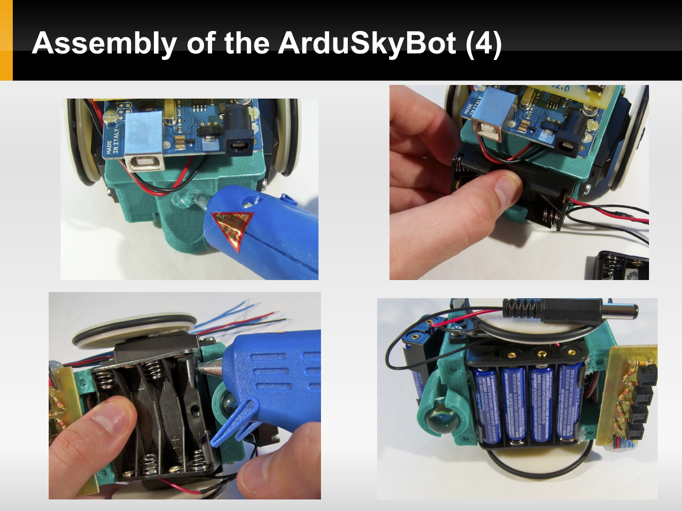
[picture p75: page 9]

## You have built an ArduSkyBot!

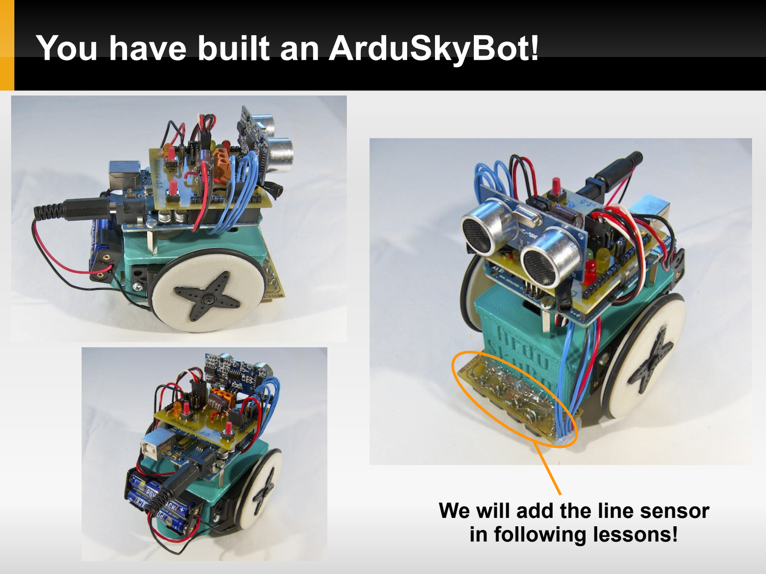
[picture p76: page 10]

We will add the line sensor in following lessons!

## Now we can begin with the programming!

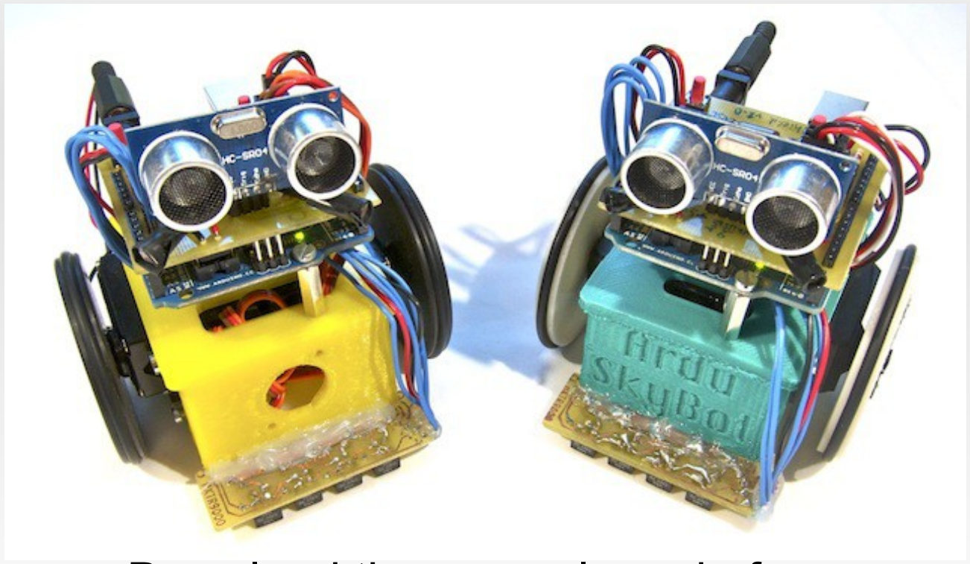
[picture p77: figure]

## Download the example code from http://www.carlosgs.es/2012-summer-workshop

## License

### This work is licensed under the

## Attribution - Share Alike

Creative Commons license.

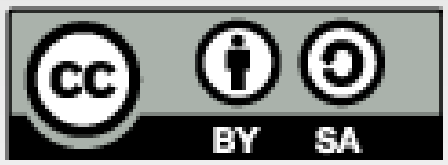
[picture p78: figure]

http://creativecommons.org/licenses/by-sa/3.0/

### Author:

## Carlos García Saura

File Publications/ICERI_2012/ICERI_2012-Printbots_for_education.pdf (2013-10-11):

## LOW COST EDUCATIONAL PLATFORM FOR ROBOTICS, USING OPEN-SOURCE 3D PRINTERS AND OPEN-SOURCE HARDWARE

### Carlos García-Saura¹

### , Juan González-Gómez²

1 Escuela Politécnica Superior, Universidad Autónoma de Madrid (SPAIN)
2 Robotics and Cybernetics Group, Universidad Politécnica de Madrid (SPAIN) carlos.garciasaura@estudiante.uam.es, jggomez@etsii.upm.es

### Abstract

In this paper, we present a new design methodology for educational robotic platforms. Using printbots (open-source 3D-printable robots) as a starting point in our designs has allowed us to create custom robots with very little effort. Using this new methodology we have designed the ArduSkybot, a robot that has enough features for its usage at different educational levels while keeping a very reduced cost. The robot is based on Arduino and the Printshield, our new electronics platform. It provides integration of various sensors (light, distance and line sensors) and actuators (motors, lights and speaker). It is also easy to expand by students and researchers. We describe our designs, and document their performance in various workshops with college, primary and secondary students. Our methodology is described and suggestions are given regarding future printbot-based workshops. Keywords: Printbot, robotic platform, 3D printing, Arduino, open-source, open-hardware, low cost.

### 1 INTRODUCTION

Robots have been successfully used for educational purposes during decades. The main advantage of teaching Robotics is that it is an interdisciplinary field that involves mechanics, electronics and programming. Students can learn from all these subjects at the same time, while having fun building robots. According to [1], a robotic platform should be cheap (to allow one robot per student or working in small groups), easy to repair (since we will be working with a large number of them), and flexible enough to allow expandability. In [2] it is suggested that educational robots should not only allow education but also provide enough features to allow research, even in its basic versions. Other authors [3] highly recommend the use of real robots instead of simulated environments, showing that it is possible to do really impressive amount of work in a robotics introductory course even with simple platforms. For instance, at Universidad Autónoma de Madrid our simple custom-designed robot (the Skybot¹
) has been used since 2004 to give robotics lessons with great results.
Robotic platforms can be divided in two main groups: commercial and custom. Commercial educational robots are usually the easiest option for teachers, since there is a wide variety available on the market [2]. Prices range from 100€ to 4500€ per robot. Each design has different features such as big processing power, multiple sensors, simple logic and so forth. The teacher has to evaluate these platforms according to the required features and price constrains. A very popular platform is the LegoTM NXT²
[1,4,5]. The main disadvantage of commercial platforms is that they are closed and proprietary. Students can use them as black boxes, but the manufacturer doesn't allow to study how they have been designed. Hence, students cannot easily extend or modify commercial designs. As an additional disadvantage, the company may decide to discontinue that robot design (when they create a new version, for example). In that case, teachers should search for a new robot and re-write a new robotic course.
The other group comprises custom robots. Main advantages of custom-designed robots are that teachers or Universities fully own the robot design and therefore can decide what upgrades to do. They can adapt the robot for its use in different subjects, and students can also learn the whole robot design process. Some examples of fully-custom robots are the e-puck [2] and the RobEx [6]. On the other hand, custom robots are usually more expensive, and it takes more time to write a course since the robot has to be designed and built previously. For that reason, some authors have chosen a mixed

1
http://www.iearobotics.com/wiki/index.php?title=Skybot

2
http://mindstorms.lego.com

Proceedings of ICERI2012 Conference
19th-21st November 2012, Madrid, Spain

ISBN: 978-84-616-0763-1 2699 approach were commercial kits are used for the mechanics, and then custom electronics are added. One example is [3], based on the Parallax Boe-Bot³
robot.
A new approach was taken with the Miniskybot robot [7], were the concept of printbot was presented. These are 3D-printable open-source robots. They can be easily built on open-source 3D printers⁴
at a
very low cost. Therefore, printbots are low cost easy-to-build custom robots. Furthermore, as printbots are open, communities have grown around them, sharing the designs. This has given users the ability to improve their robots and adapt them to their needs. The result is that printbots are already evolving and diversifying. This is shown in sites like Thingiverse, where more than 75 printbots have emerged: from simple wheeled robots to complex four-legged robots or even robotic arms⁵
Usage of printbots for educational purposes was covered in [8]. It was shown that these kind of robots are a very good tools to stimulate students and develop their creativity. For the first time ever, students can easily expand the capabilities of the robots they are given.
Now there is a new alternative for universities and teachers who need to choose a robotic platform. Instead of buying a commercial robot or designing a custom robot from scratch, they can choose an already existing printbot design and create a derivative robot.
In this paper, we present our new 3D-printable robotic platform for education and research. It has been designed using this new methodology based on printbots. Section 2 covers the election of adequate electronics. Section 3 explains the design process of the ArduSkybot. Section 4 shows the results of using our robotic platform as an educational tool. Section 5 discusses the new methodology used. Finally, the conclusions and future work are given.

### 2 ELECTRONICS WITH ARDUINO

Each robotic platform includes its own controlling board. Electronics are usually commercial, such as the brick used in LegoTM NXT, the BasicStamp⁶

from Parallax [3] or the Dwengo-board⁷ [1]. Some
others are custom boards based on micro-controllers (Atmel, Microchip and so forth). This has resulted in an heterogeneous landscape of electronic boards for robotic education.
Arduino⁸
is one of the most popular and fastest growing generic-purpose electronics platform. It is based on Atmel micro-controllers and offers a wide variety of boards with an standardized programming interface, simplifying the first contact with electronics while being powerful enough for its use in any kind of project.
Some interesting conclusions have been stated in [9]. First, it shows that students that use Arduino usually come up with more creative projects than students that use other platforms (this is due to the high availability of Arduino kits, good documentation and support forums). Second, it gives a warning: the Arduino community is usually focused in making things work, rather than choosing the optimal way to implement them. When teaching specific low-level optimization it is usually better to switch to other platforms. An example on how to use Arduino with educational robots is presented in [10], where they take the results obtained in [3] with the Boe-Bot and solve the complexity of the electronics (and programming) by replacing them with an Arduino board.
In addition, Arduino is open-hardware. All the designs are available for anyone to use, study or modify. Furthermore, Arduino has a huge community of people that develop tools (both software and hardware), share their projects and give support.
For these reasons, we have chosen to use Arduino in our robots.

### 2.1 Usage of shields for a better integration

As we have mentioned before, Arduino is a general purpose board. It only provides I/O pins, so we can't use it directly in our robots: we need to provide external circuitry in order to connect sensors and

3
http://www.parallax.com/go/boebot

4
http://reprap.org/wiki/Main_Page

5
http://www.thingiverse.com/thing:18264, http://www.thingiverse.com/thing:18045 and http://www.thingiverse.com/thing:30163

6
http://www.parallax.com/BASICStampGeneralInformation/tabid/214/Default.aspx

7
http://www.dwengo.org/products/dwengo-board

8
http://arduino.cc actuators. Using prototype boards usually ends with a mess of wires and connections (an example is shown in Fig 2.1). These kind of solutions work very well and are a good way to teach low-level electronics, but the resulting circuits are usually far away from being robust and compact.
Thanks to the Arduino community, there are plenty of “shield” designs available⁹
. These are circuit
boards that are designed to easily fit on the top of an Arduino board. One example of how these shields are plugged is shown in Fig. 2.1. We are going to set our focus on the Arduino UNO board since it is the most simple and widespread, to the point that it can be considered as the standard.

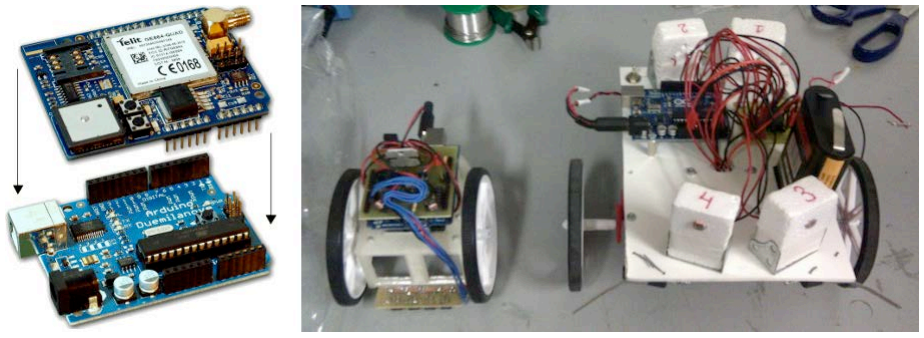
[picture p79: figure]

Fig. 2.1 Example shield (left) and a practical case of compacting circuitry (right)

This huge variety of shields (Wi-Fi shield, motor shield, GPS shield and more) is intended to provide an easy way to interact with many different peripherals simplifying electronic connections. However, we haven't been able to find a commercially-available shield intended for robotics. None of them offers a good way to plug the amount of sensors, motors and extension connectors required to build a compact full-featured robot.
Our solution was to use custom-designed shields (like the CRM-Shield mounted on the HKTR-9000 that is shown in Fig. 2.1), described with detail in next section.

### 3 DESIGNING OUR ROBOT

One of the great advantages of using printbots is that they can be redesigned to utilize available resources. For our first robotic workshop at the Robotics and Mechatronics Club we wanted to make use of components that we already had available: many different sensors, lots of Arduino UNO boards, some Pololu micro-motors¹⁰ with compatible wheels, a few ball casters, screws and so on.

Regarding the electronics, we concluded that the best solution was to custom-design our own shield focusing on robotics. The main requirements were to provide a good integration in order to reduce size and complexity, and to make robust electronics. As we like working with open-source, Kicad has been used to design the boards. We have developed all our printed circuit boards using simple toner transfer techniques.
Our first approach resulted in the CRM-Shield. This shield integrates two light sensors, one LED, an L298 motor driver and provided an easy way to connect a line sensor.
We were able to design our custom 3D-prinable chassis in a few hours, and the full robot prototype of the HKTR-9000¹¹ (Fig. 3.1) was working the next week. Only one week after that, we had five of these robots assembled. The additional cost for out robotics club was zero, since we already had all the required parts, and the 3D printed plastic cost was marginal.
The CRM-Shield didn't even have push buttons. Light sensors were connected to a pin header and were easily taken apart. Also, the motor driver used many of the space and pins available on the

9
http://shieldlist.org
10 | http://www.pololu.com/catalog/category/60
11 | http://www.thingiverse.com/thing:23593

Arduino. Nevertheless, the CRM-Shield behaved surprisingly well in our first workshop (view Section 4.1).

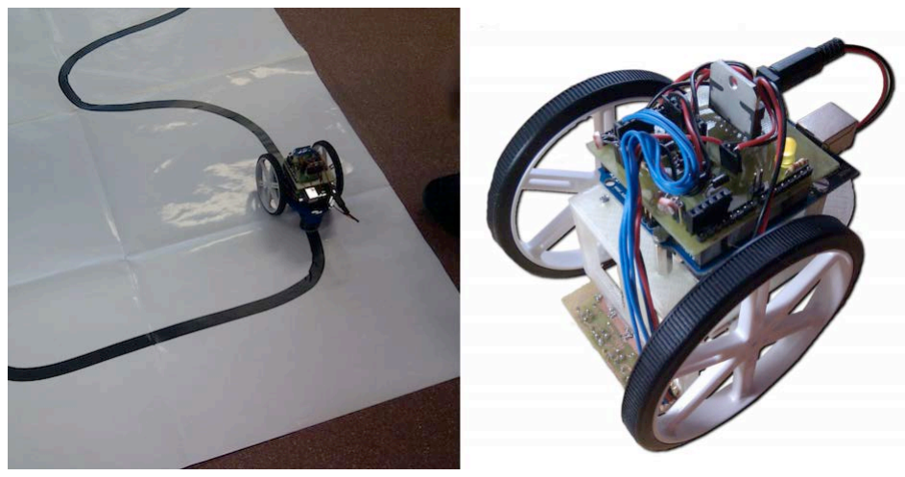
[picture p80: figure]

Fig. 3.1 HKTR-9000 possible usage as a line follower (left) and detail view (right)

Encouraging results obtained with the CRM-Shield prompted us to re-design it trying to fix existing problems: The Printshield (Fig. 3.2) was the result of our efforts. We decided to switch back to continuous rotation servos (like the ones used in the original MiniSkybot) since they don't require a motor driver, but only one digital pin to be driven. Easy to use motors and a standardized connector allow an easy expandability. Two push-buttons were added (reset and function) and we found a much robust way to attach light sensors using a screw terminal instead of pin headers.

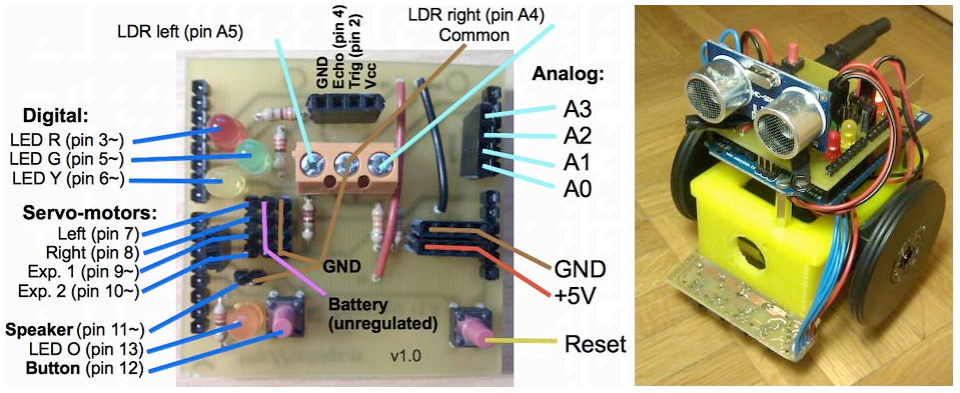
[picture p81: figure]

Fig. 3.2 Printshield connection diagram (left) and usage example in the ArduSkybot (right)

Printshield integrates many LEDs (that are very good to teach basic programming as they serve for debugging purposes), various sensors (light and distance), and provides an easy way to connect peripherals (servo motors, speaker, line sensors and more).
The Printshield uses very common electronic components and thus is very cheap (around 5€ per board). It is also very easy to reuse in other printbots.
ArduSkybot¹² uses the 3D printable chassis and wheels from the MiniSkybot v2.0¹³. As a result, we have created a simple mobile platform that benefits from the Printshield providing many sensors (distance, light and line sensor), two motors (continuous rotation servos), LED lights, push-buttons and a speaker.
12 | http://www.thingiverse.com/thing:26818
13 | https://github.com/Obijuan/Miniskybot

The production cost has been kept really low (around 55€), which is very similar to the price of the MiniSkybot shown in [7]. Later on, we have validated the educational capabilities of the ArduSkybot in a small workshop.

### 4 VALIDATION OF THE NEW PLATFORM

We have tested our printbot designs in two workshops: one with college students and the other one with primary and secondary students.

### 4.1 Robotics introductory course with the HKTR-9000

The Robotics introductory course¹⁴ took place the 23, 24, 25, 28 and 29 of May 2012, and was organised by the Robotics and Mechatronics Club at Universidad Autónoma de Madrid.
4.1.1 Target and group characteristics
The workshop was aimed to a group of 20 engineering students (18 to 23 years old). The target was to give an introduction on basic robotics. We didn't require any robotics knowledge prior to the workshop: they learnt the basics (electronics with Arduino and the CRM-Shield, and simple mechanics), and built a total of five HKTR-9000 robots. They already had experience with at least one programming language.
4.1.2 Duration and workflow
This workshop had a length of 15 hours, divided in five sessions of three hours each. Workflow consisted in an initial 20 minute explanation, and after that students had to solve the proposed exercises. They worked in five groups following the provided instructions. Regarding material resources, we used a laboratory with computers, a projector for presentations, and five HKTR-9000 kits that were made previously.
4.1.3 Workshop contents
First two lessons explained the basic components of a robot, and Arduino was introduced. Students learned how to use sensors and motors at a low level using prototype boards. After that, they programmed the required functions for controlling the motors.
Next two lessons included the assembly of the HKTR-9000 and some programming examples. Students learned how to make the robot follow a light source, and some basic PD control algorithms in order to make the robot follow a black line.
Final lesson was left for students to decide what to do, providing them with distance sensors and speakers. They came up with very creative ideas: for example, some students were able to get the robot to avoid obstacles while playing sounds, and others made the robot follow light and play notes according to the distance read by the sensor.
4.1.4 Results
During the workshop, some students asked for a reduction of theoretical content while others were missing more complex exercises. The solution was to simplify the presentations and also the exercises while providing additional ones for advanced students.
We found that is was really hard to install the distance sensor in the HKTR-9000. This was the main reason for the later integration of this sensor in the Printshield.
The workshop was a success, since students were very satisfied at the end and all the program was covered. It also motivated some students to join the robotics club, which is also a very good sign.

### 4.2 ArduSkyBot 2012 Summer Workshop

The ArduSkyBot 2012 Summer Workshop¹⁵ took place from July 30 to August 2 in Palo Alto, and was organised by Carlos García Saura.

14 | http://spock.ii.uam.es/actividades/taller-de-iniciacion-a-la-robotica
15 | http://carlosgs.es/2012-summer-workshop

4.2.1 Target and group characteristics
The target was to give an introduction on robotics to a small group of four 12-14 year old kids. They learnt the basics of robotics (electronics with Arduino and Printshield, programming and mechanics), built their own ArduSkyBot and made their own program modifications.
4.2.2 Duration and workflow
This workshop had a length of roughly 10 hours, divided in four lessons of two and a half hours each. Workflow consisted in an initial 15-30 minute explanation, and after that we gave the students some example code and simple exercises that they had to solve (giving additional ones for advanced students, as we had learned from the previous workshop), helping them when they needed so. Regarding material resources, we used two tables, a display for presentations and four ArduSkyBot kits. Students were required to bring their own laptop, and an Arduino board with its USB cable.
4.2.3 Workshop contents
First lesson included the explanation of what is a robot and what are its main components. Arduino was presented, together with the Printshield, and students assembled and tested basic examples with LEDs and audio tones.
Next two lessons included the introduction of the ArduSkybot and its assembly. They first made the robot move modifying basic code examples. We gradually presented them with more complex examples as following light or avoiding obstacles. Some students solved the advanced exercise, managing to make the robot follow light while avoiding obstacles.
In the last lesson, the line sensor was provided and students were able to make the robot follow a black line. The proposed challenge was to avoid an obstacle while following a line, and then returning to the path. We were amazed to see that some students succeeded on this!
4.2.4 Results
For the preparation of the lessons for this workshop we followed the recommendations given in [4] for working with small kids: since it is much different than working with college students it required a different approach.
We structured the lessons in a very simple way, first exposing what they would learn and using an example-based system. Yet, smaller kids said that everything was extremely complex! It is very important to simplify things a lot when working with small kids.
One interesting discovery was that kids love using the speaker: they had lots of fun just by changing the playback speed of the melody example given. Also, when using the measurements from the distance sensor to generate tones they were amazed by this new musical instrument. The speaker was present during the whole workshop, and the buzzer-like sounds helped to create a friendly work environment for the kids.
As we have said, kids were required to bring their own Arduino board. We decided this after seeing that they already had an Arduino kit at home (we confirmed this was their parents failed attempt to get them into electronics). This fact cut production cost of the robots to more than a half (around 25€) since the Arduino board is the most expensive part. Thanks to the low price of the parts we were able to let kids take the robot home at the end of the course, which made them really happy.

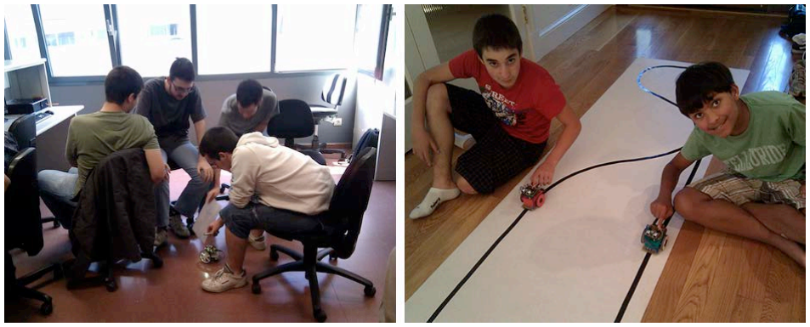
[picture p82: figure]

Fig 4.1 Robotics introductory course (left) and ArduSkybot 2012 summer workshop (right)

### 5 DISCUSSION

It took a surprisingly small amount of time to set up the HKTR-9000 and the ArduSkybot for our workshops. Taking in account that the assembly process of the large robot that appears in Fig. 2.1 took us about two weeks, we were really impressed when we saw that we were able to design and produce five HKTR-9000 robots in that same period of time.
Our experience with the ArduSkybot has been even more impressive: The design and manufacture process for five of them (including the prototype) took around one week.
The ArduSkybot was designed as a derivative of the existing MiniSkybot, and the final cost is very similar (around 55€). For this reason, we must indicate the improvements that were made:
- Now the robot is based on Arduino UNO, and it is possible to connect with USB directly. Many people already have one of these boards, and that drops down the price of the robot since they only need to add the cheap Printshield and sensors.
- A line sensor has been added. It is made with four CNY70 infra-red sensors.
- Integrated light sensor, made of two LDR firmly attached using a screw terminal.
- Easy to use integrated distance sensor, using a cheap SR-04 module.
- Finally, it has two pulse-buttons, some LED lights and a piezoelectric buzzer.
Using a 3D printer has allowed the fast replication of our robots, but using printbots as a start point has been the key for an accelerated custom design process. More importantly, we have used the resulting robots in various workshops that have shown positive results. We truly believe this kind of approaches will mean a revolution in how robotic courses are given.

### 6 CONCLUSIONS AND FUTURE WORK

Our new printrbot-based methodology has been proven to work: robotic courses aren't restricted to use commercial robotic platforms, nor design their robots from scratch any more. Using printbots as a starting point, it is possible to design custom educational robots with very little effort and great results. The ArduSkybot has been developed using this new methodology, and Printshield is our answer to the lack of Arduino shields that are specific for robotics. It provides a compact solution for integrating basic sensors and actuators in Arduino-based robots like the ArduSkybot.
As future work, we want to keep improving these kind of robots. Using tracks instead of wheels will increase stability, and a new version of the Printshield will have infra-red connectivity to allow communication between robots and therefore the study of more complex algorithms.
All the documentation and designs required to build our designs are available online as open-source. We have also published all the slides and exercises used in our workshops.

Updates on our work and all related resources can be found in our websites: http://www.carlosgs.es and http://www.iearobotics.com.

### ACKNOWLEDGEMENTS

We want to thank the Robotics and Mechatronics Club at Universidad Autónoma de Madrid for providing the material resources, as well as Mr. Lucas Polo and Mr. Miguel Gargallo for their direct collaboration in the organization of the course. We are also thankful to Mrs. Carmen Saura for providing the workspace and helping in the organization of our robotic course in Palo Alto.

### REFERENCES

[1] Wyffels, F., Hermans, M. & Schrauwen, B. (2010), "Building robots as a tool to motivate students into an engineering education", In Proceedings of the 1st international conference on Robotics in Education, RiE2010. September 2010. pp. 49-52. FEI STU, Slovakia.
[2] Mondada, F., Bonani, M., Raemy, X., Pugh, J., Cianci, C., Klaptocz, A., Magnenat, S., Zufferey, J.-C., Floreano, D. and Martinoli, A. (2009), “The e-puck, a Robot Designed for Education in Engineering”, Proceedings of the 9th Conference on Autonomous Robot Systems and Competitions, 1(1) pp. 59-65.
[3] Balogh, R. (2008) “Basic Activities with the Boe-Bot Mobile Robot”, In DidInfo2008. 14th International Conference. FPV UMB, Banská Bystrica, Slovakia.
[4] Peter van Lith (2007), "Teaching Robotics in Primary and Secondary schools", ComLab Conference 2007, November 30 - December 1, Radovljica, Slovenia.
[5] Carter, J. & Coupland, S. (2010), "Teaching Robotics at the Postgraduate Level: Delivering for On Site and Distance Learning Students", In Proceedings of the 1st international conference on Robotics in Education, RiE2010. September 2010., pp. 149-154. FEI STU, Slovakia.
[6] J. Mateos, A. Sánchez, Luis J. Manso, Pilar Bachiller, Pablo Bustos (2010), "RobEx: an open-hardware robotics platform". Proceedings, Workshop en Agentes Físicos (WAF2010), Valencia, Spain.
[7] Juan Gonzalez-Gomez, Alberto Valero-Gomez, Andres Prieto-Moreno, Mohamed Abderrahim (2011), "A New Open Source 3D-printable Mobile Robotic Platform for Education", Proc. of the 6th International Symposium on Autonomous Minirobots for Research and Edutainment, May, 23-25, Bielefeld, Germany.
[8] A. Valero, J. González-Gómez, V. Gonzalez, M.A. Salichs (2012), “Printable Creativity in Plastic Valley UC3M”. IEEE Educon 2012. Marrakech. Morocco. Apr, 2012.
[9] P. Jamieson (2011) “Arduino for teaching embedded systems. Are computer scientists and engineering educators missing the boat?”, International Conference on Frontiers in Education: Computer Science and Computer Engineering.
[ 1 0 ] Balogh, R. (2010), "Educational Robotic Platform based on Arduino", In Proceedings of the 1st international conference on Robotics in Education, RiE2010. September 2010., pp. 119-122. FEI STU, Slovakia.

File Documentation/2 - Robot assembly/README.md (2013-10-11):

ArduSkybot assembly  
=====  

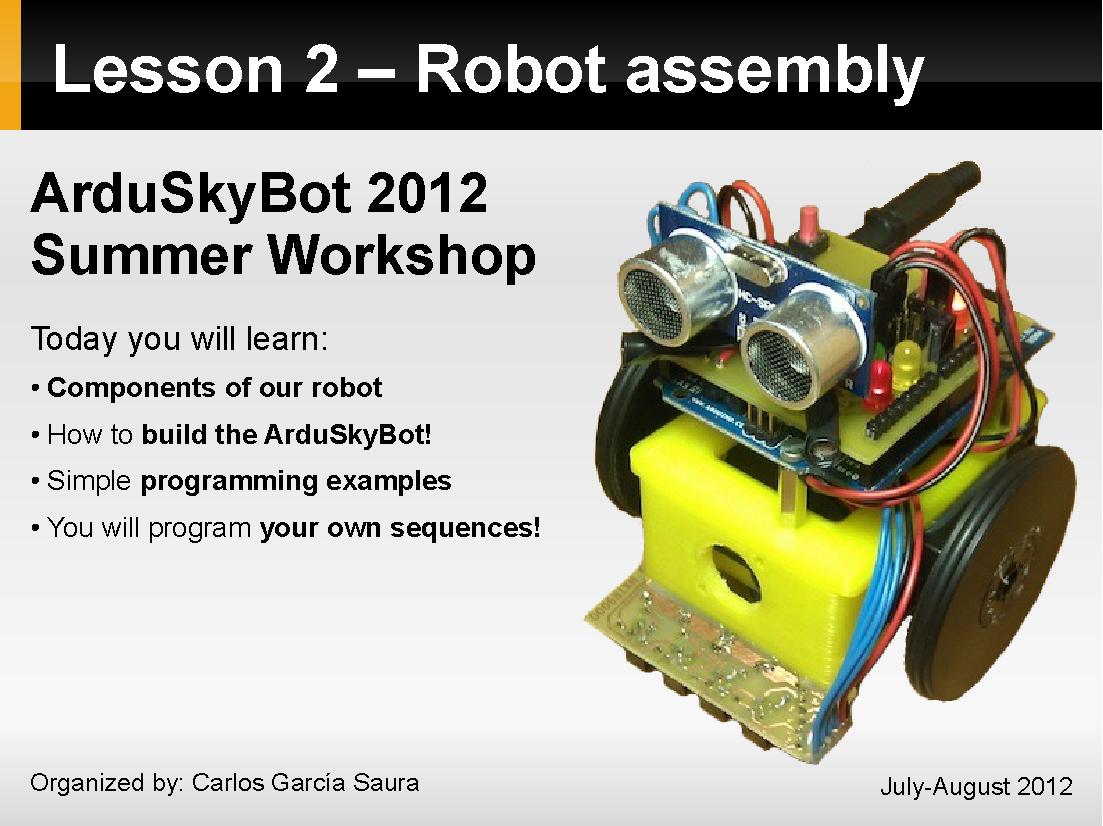
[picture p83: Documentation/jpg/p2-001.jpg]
  
  
  
  
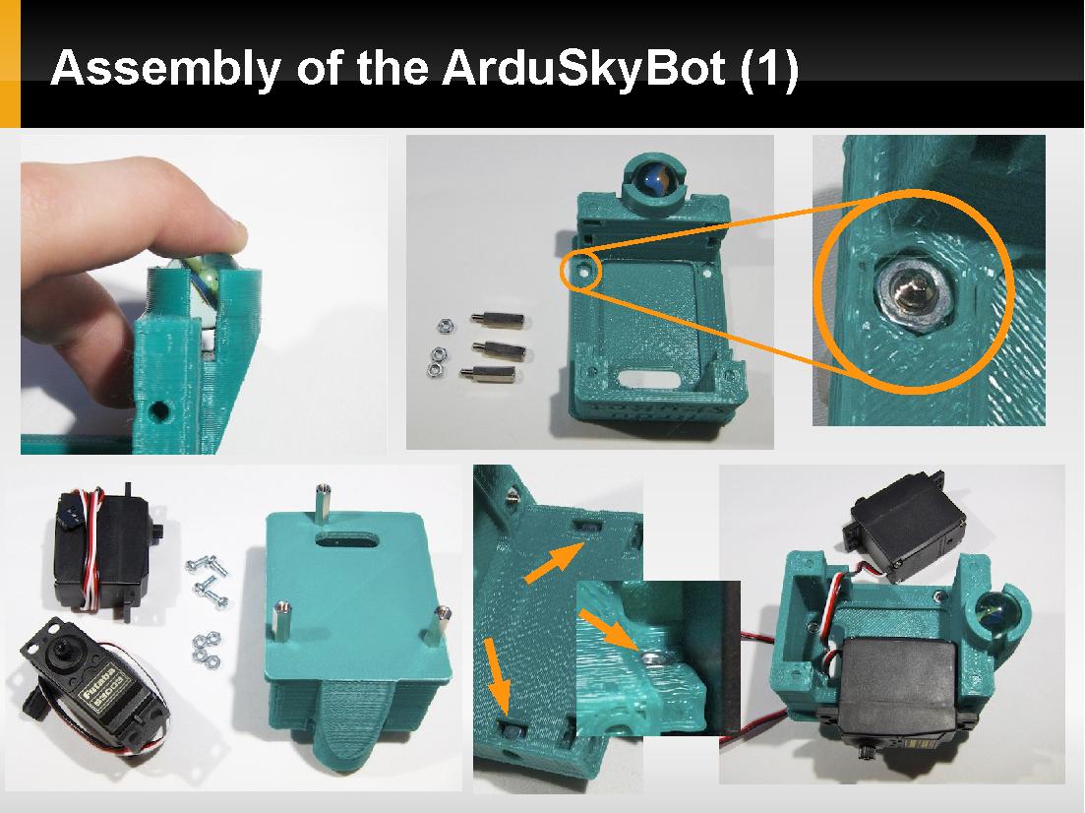
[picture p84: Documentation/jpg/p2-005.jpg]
  
  
  
  
  
  
  


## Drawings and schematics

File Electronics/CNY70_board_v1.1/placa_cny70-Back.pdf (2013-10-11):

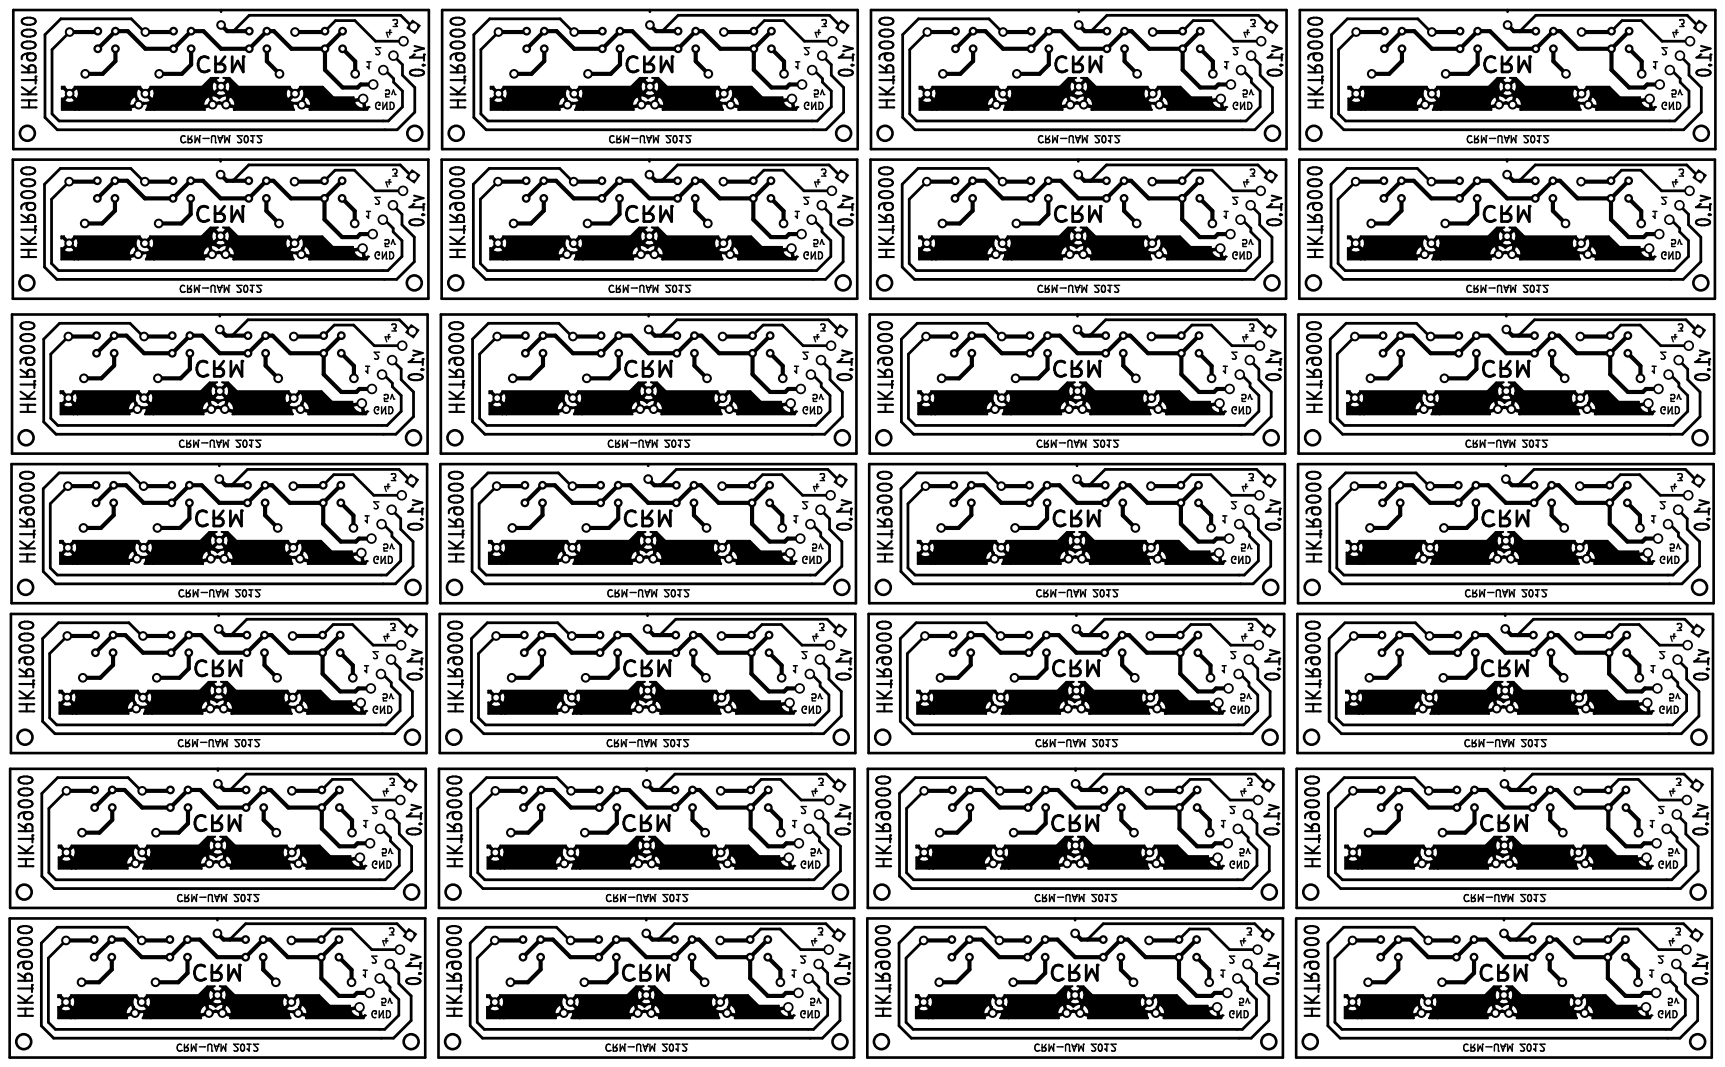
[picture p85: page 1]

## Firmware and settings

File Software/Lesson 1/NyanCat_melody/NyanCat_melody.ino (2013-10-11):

/*
 Nyan Cat
 
 Plays Nyan Cat
 example to fast (old version): http://www.youtube.com/watch?v=eFHfGA5e4n8
 example this version: http://youtu.be/t3gKFuTb4kQ
 circuit:
 * 8-ohm speaker on digital pin 8
 
 By: Bruce Helsen (geobruce) 
 Stan Draulans (purewantfun)
 update (Jrigvd (Jordy v. D.))
 */
#include "pitches.h"

// --- PIN DEFINITIONS ---

#define LED_RED 3      // LED Lights
#define LED_GREEN 5
#define LED_YELLOW 6
#define LED_ORANGE 13

#define SPEAKER 11

#define BUTTON 12

// --- LEDs ---

// Function for initiating the pins used by the LEDs
void init_LED_pins() {
  pinMode(LED_RED,OUTPUT);
  pinMode(LED_GREEN,OUTPUT);
  pinMode(LED_YELLOW,OUTPUT);
  pinMode(LED_ORANGE,OUTPUT);
}

// --- BUTTON ---

// Function for initiating the pin used by the button
void init_button_pin() {
  pinMode(BUTTON,INPUT);

  digitalWrite(BUTTON, HIGH); // Enable internal pull-up resistor
}

// Function for reading the button value
// Returns 1 if the button is being pressed, 0 if it is not
int button_is_pressed() {
  return !digitalRead(BUTTON);
}

int intro[] = {
  //intro
  NOTE_DS5,
  NOTE_E5,
  NOTE_FS5,
  NOTE_B5,
  NOTE_DS5,
  NOTE_E5,
  NOTE_FS5,
  NOTE_B5,
  NOTE_CS6,
  NOTE_DS6,
  NOTE_CS6,
  NOTE_AS5,
  NOTE_B5,
  NOTE_FS5,
  NOTE_DS5,
  NOTE_E5,
  NOTE_FS5,
  NOTE_B5,
  NOTE_CS6,
  NOTE_AS5,
  NOTE_B5,
  NOTE_CS6,
  NOTE_E6,
  NOTE_DS6,
  NOTE_E6,
  NOTE_B5, 

};

// note durations: 4 = quarter note, 8 = eighth note, etc.:
int noteDurations[] = {
  16,
  16,
  8,
  8,
  16,
  16,
  16,
  16,
  16,
  16,
  16,
  16,
  8, //13
  8,
  16,
  16,
  8,
  8,
  16,
  16,
  16,
  16,
  16,
  16,
  16,
  16 //25 intro
};

void setup() {
  init_button_pin();
  init_LED_pins();

  // Wait until the button is pressed
  while( button_is_pressed() == 0 ) {
    delay(100);
  }

  // We turn on the ORANGE LED so we know our program is running
  digitalWrite(LED_ORANGE, HIGH);

  for (int thisNote = 0; thisNote < 25; thisNote++) {

    // to calculate the note duration, take one second 
    // divided by the note type.
    //e.g. quarter note = 1000 / 4, eighth note = 1000/8, etc.
    int noteDuration = 1500/noteDurations[thisNote];
    tone(SPEAKER, intro[thisNote],noteDuration);

    // to distinguish the notes, set a minimum time between them.
    // the note's duration + 30% seems to work well:
    int pauseBetweenNotes = noteDuration * 1.30;
    delay(pauseBetweenNotes);
    // stop the tone playing:
    noTone(SPEAKER);
  }
}
int melody[] = {
  //A
  NOTE_FS5,
  NOTE_GS5,
  NOTE_DS5,
  NOTE_DS5,
  REST,
  NOTE_B4,
  NOTE_D5,
  NOTE_CS5,
  NOTE_B4,
  REST,
  NOTE_B4,
  NOTE_CS5,
  NOTE_D5,
  NOTE_D5,
  NOTE_CS5,
  NOTE_B4,
  NOTE_CS5,
  NOTE_DS5,
  NOTE_FS5,
  NOTE_GS5,
  NOTE_DS5,
  NOTE_FS5,
  NOTE_CS5,
  NOTE_DS5,
  NOTE_B4,
  NOTE_CS5,
  NOTE_B4,
  NOTE_DS5,
  NOTE_FS5,
  NOTE_GS5,
  NOTE_DS5,
  NOTE_FS5,
  NOTE_CS5,
  NOTE_DS5,
  NOTE_B4,
  NOTE_D5,
  NOTE_DS5,
  NOTE_D5,
  NOTE_CS5,
  NOTE_B4,
  NOTE_CS5,
  NOTE_D5,
  NOTE_B4,
  NOTE_CS5,
  NOTE_DS5,
  NOTE_FS5,
  NOTE_CS5,
  NOTE_DS5,
  NOTE_CS5,
  NOTE_B4,
  NOTE_CS5,
  NOTE_B4,
  NOTE_CS5,
  NOTE_FS5,
  NOTE_GS5,
  NOTE_DS5,
  NOTE_DS5,
  REST,
  NOTE_B4,
  NOTE_D5, 
  NOTE_CS5,
  NOTE_B4,
  REST,
  NOTE_B4,
  NOTE_CS5,
  NOTE_D5,
  NOTE_D5,
  NOTE_CS5,
  NOTE_B4,
  NOTE_CS5,
  NOTE_DS5,
  NOTE_FS5,
  NOTE_GS5,
  NOTE_DS5,
  NOTE_FS5,
  NOTE_CS5,
  NOTE_DS5,
  NOTE_B4,
  NOTE_CS5,
  NOTE_B4,
  NOTE_DS5,
  NOTE_FS5,
  NOTE_GS5,
  NOTE_DS5,
  NOTE_FS5,
  NOTE_CS5,
  NOTE_DS5,
  NOTE_B4,
  NOTE_D5,
  NOTE_DS5,
  NOTE_D5,
  NOTE_CS5,
  NOTE_B4,
  NOTE_CS5,
  NOTE_D5,
  NOTE_B4,
  NOTE_CS5,
  NOTE_DS5,
  NOTE_FS5,
  NOTE_CS5,
  NOTE_DS5,
  NOTE_CS5,
  NOTE_B4,
  NOTE_CS5,
  NOTE_B4,
  NOTE_CS5,
  //end of loop
  NOTE_B4,
  NOTE_FS4,
  NOTE_GS4,
  NOTE_B4,
  NOTE_FS4,
  NOTE_GS4,
  NOTE_B4,
  NOTE_CS5,
  NOTE_DS5,
  NOTE_B4,
  NOTE_E5,
  NOTE_DS5,
  NOTE_E5,
  NOTE_FS5,
  NOTE_B4,
  NOTE_B4,
  NOTE_FS4,
  NOTE_GS4,
  NOTE_B4,
  NOTE_FS4,
  NOTE_E5,
  NOTE_DS5,
  NOTE_CS5,
  NOTE_B4,
  NOTE_FS4,
  NOTE_DS4,
  NOTE_E4,
  NOTE_FS4,
  NOTE_B4,
  NOTE_FS4,
  NOTE_GS4,
  NOTE_B4,
  NOTE_FS4,
  NOTE_GS4,
  NOTE_B4,
  NOTE_B4,
  NOTE_CS5,
  NOTE_DS5,
  NOTE_B4,
  NOTE_FS4,
  NOTE_GS4,
  NOTE_FS4,
  //
  NOTE_B4,
  NOTE_B4,
  NOTE_AS4,
  NOTE_B4,
  NOTE_FS4,
  NOTE_GS4,
  NOTE_E4,
  NOTE_E5,
  NOTE_DS5,
  NOTE_E5,
  NOTE_FS5,
  NOTE_B4,
  NOTE_AS4,
  //
  NOTE_B4,
  NOTE_FS4,
  NOTE_GS4,
  NOTE_B4,
  NOTE_FS4,
  NOTE_GS4,
  NOTE_B4,
  NOTE_CS5,
  NOTE_DS5,
  NOTE_B4,
  NOTE_E5,
  NOTE_DS5,
  NOTE_E5,
  NOTE_FS5,
  NOTE_B4,
  NOTE_B4,
  NOTE_FS4,
  NOTE_GS4,
  NOTE_B4,
  NOTE_FS4,
  NOTE_E5,
  NOTE_DS5,
  NOTE_CS5,
  NOTE_B4,
  NOTE_FS4,
  NOTE_DS4,
  NOTE_E4,
  NOTE_FS4,
  NOTE_B4,
  NOTE_FS4,
  NOTE_GS4,
  NOTE_B4,
  NOTE_FS4,
  NOTE_GS4,
  NOTE_B4,
  NOTE_B4,
  NOTE_CS5,
  NOTE_DS5,
  NOTE_B4,
  NOTE_FS4,
  NOTE_GS4,
  NOTE_FS4,
  NOTE_B4,
  NOTE_B4,
  NOTE_AS4,
  NOTE_B4,
  NOTE_FS4,
  NOTE_GS4,
  NOTE_B4,
  NOTE_E5,
  NOTE_DS5,
  NOTE_E5,
  NOTE_FS5,
  NOTE_B4,
  NOTE_CS5 

};
int melodyNoteDurations[] = {
  //a
  8,
  8,
  16,
  16,
  16,
  16,
  16,
  16,
  16,
  16,
  8,
  8,
  8,
  16,
  16,
  16,
  16,
  16,
  16,
  16,
  16,
  16,
  16,
  16,
  16,
  16,
  16,
  8,
  8,
  16,
  16,
  16,
  16,
  16,
  16,
  16,
  16,
  16,
  16,
  16,
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
  //
  8,
  16,
  16,
  8,
  16,
  16,
  16,
  16,
  16,
  16,
  16,
  16,
  16,
  16,
  8,
  8,
  16,
  16,
  16,
  16,
  16,
  16,
  16,
  16,
  16,
  16,
  16,
  16,
  8,
  16,
  16,
  8,
  16,
  16,
  16,
  16,
  16,
  16,
  16,
  16,
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
  //
  8,
  16,
  16,
  16,
  16,
  16,
  16,
  16,
  16,
  16,
  16,
  8,
  8,
  //
  8,
  16,
  16,
  8,
  16,
  16,
  16,
  16,
  16,
  16,
  16,
  16,
  16,
  16,
  8,
  8,
  16,
  16,
  16,
  16,
  16,
  16,
  16,
  16,
  16,
  16,
  16,
  16,
  8,
  16,
  16,
  8,
  16,
  16,
  16,
  16,
  16,
  16,
  16,
  16,
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
  //
  8,
  16,
  16,
  16,
  16,
  16,
  16,
  16,
  16,
  16,
  16,
  8,
  8 
};
void loop() {


  // iterate over the notes of the melody:
  for (int thisNote = 0; thisNote < 216; thisNote++) {

    // to calculate the note duration, take one second 
    // divided by the note type.
    //e.g. quarter note = 1000 / 4, eighth note = 1000/8, etc.
    int noteDuration = 1400/melodyNoteDurations[thisNote];
    tone(SPEAKER, melody[thisNote],noteDuration);

    // to distinguish the notes, set a minimum time between them.
    // the note's duration + 30% seems to work well:
    int pauseBetweenNotes = noteDuration * 1.30;
    delay(pauseBetweenNotes);
    // stop the tone playing:
    noTone(SPEAKER);
  }
}

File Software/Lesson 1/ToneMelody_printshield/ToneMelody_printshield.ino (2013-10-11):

/*
 Printshield example code
 
 Author: Carlos Garcia Saura
 July 2012
 */
 
// File with musical notes
#include "pitches.h"

// notes in the melody:
int melody[] = {
  NOTE_C4, NOTE_G3,NOTE_G3, NOTE_A3, NOTE_G3,0, NOTE_B3, NOTE_C4};

// note durations: 4 = quarter note, 8 = eighth note, etc.:
int noteDurations[] = {
  4, 8, 8, 4,4,4,4,4 };

// --- PIN DEFINITIONS ---

#define LED_RED 3      // LED Lights
#define LED_GREEN 5
#define LED_YELLOW 6
#define LED_ORANGE 13

#define BUTTON 12

#define LDR_LEFT A5   // Pins for the light sensors
#define LDR_RIGHT A4

#define IR_1 A0       // Pins for the line sensor (four CNY70)
#define IR_2 A1       // IR_1 right, IR_4 left
#define IR_3 A2
#define IR_4 A3

#define ULTRASONIC_TRIG 2 // Pins for the ultrasonic distance sensor
#define ULTRASONIC_ECHO 4

#define SPEAKER 11


// --- ULTRASONIC SENSOR ---

// Function for initiating the pins used by the ultrasonic distance sensor
void init_pins_distance_sensor() {
  pinMode(ULTRASONIC_ECHO, INPUT);
  pinMode(ULTRASONIC_TRIG, OUTPUT);

  // Trigger pin is set low to avoid innecesary measurements
  digitalWrite(ULTRASONIC_TRIG, LOW);
}

// Function for reading the distance read by the ultrasonic sensor
// Returned value is in centimeters
int read_distance() {
  long duration;

  //This triggers the measurement
  digitalWrite(ULTRASONIC_TRIG, HIGH);
  delayMicroseconds(10);
  digitalWrite(ULTRASONIC_TRIG, LOW);

  //We receive the distance as a pulse length
  duration = pulseIn(ULTRASONIC_ECHO,HIGH);

  //Returns the distance in centimeters. 
  return duration /29 / 2 ; //use "74 / 2" for inches
}


// --- LEDs ---

// Function for initiating the pins used by the LEDs
void init_LED_pins() {
  pinMode(LED_RED,OUTPUT);
  pinMode(LED_GREEN,OUTPUT);
  pinMode(LED_YELLOW,OUTPUT);
  pinMode(LED_ORANGE,OUTPUT);
}


// --- BUTTON ---

// Function for initiating the pin used by the button
void init_button_pin() {
  pinMode(BUTTON,INPUT);

  digitalWrite(BUTTON, HIGH); // Enable internal pull-up resistor
}

// Function for reading the button value
// Returns 1 if the button is being pressed, 0 if it is not
int button_is_pressed() {
  return !digitalRead(BUTTON);
}

void wait_until_button_is_pressed() {
  while( button_is_pressed() == 0 ) delay(100);
}

void setup() {                
  // Pin initialization
  init_pins_distance_sensor();
  init_LED_pins();
  init_button_pin();

  // Wait until the button is pressed
  while( button_is_pressed() == 0 ) {
    delay(100);
  }

  // We turn on the ORANGE LED so we know our program is running
  digitalWrite(LED_ORANGE, HIGH);
}




/// WRITE YOUR CODE HERE ///
void loop() { // The loop function runs forever
  // iterate over the notes of the melody:
  for (int thisNote = 0; thisNote < 8; thisNote++) {

    // to calculate the note duration, take one second 
    // divided by the note type.
    //e.g. quarter note = 1000 / 4, eighth note = 1000/8, etc.
    int noteDuration = 1000/noteDurations[thisNote];
    tone(SPEAKER, melody[thisNote],noteDuration);

    // to distinguish the notes, set a minimum time between them.
    // the note's duration + 30% seems to work well:
    int pauseBetweenNotes = noteDuration * 1.30;
    delay(pauseBetweenNotes);
    // stop the tone playing:
    noTone(SPEAKER);
  }

  // Waits for one second
  delay(1000);

}

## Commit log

2013-10-11 Added more files
    [placa_cny70.brd, placa_cny70.sch]
2014-01-22 Nothing changed
    [ArduSkyBot_chassis_v2.3.stl, Futaba-shaft.dxf, Parameterized_battery_holder.scad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]
